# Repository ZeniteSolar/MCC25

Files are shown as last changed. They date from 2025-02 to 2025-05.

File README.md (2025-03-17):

# MCC25
MCC25  
MPPT Battery charger  

| Input Voltage | 0 ~ 21 V  |
| ---: | :--- |
| Output Voltage  | 21 ~ 40V  |
| Output Power | 200 W |
| Efficiency | > 90% |

## Modelo 3D

<p align="center">
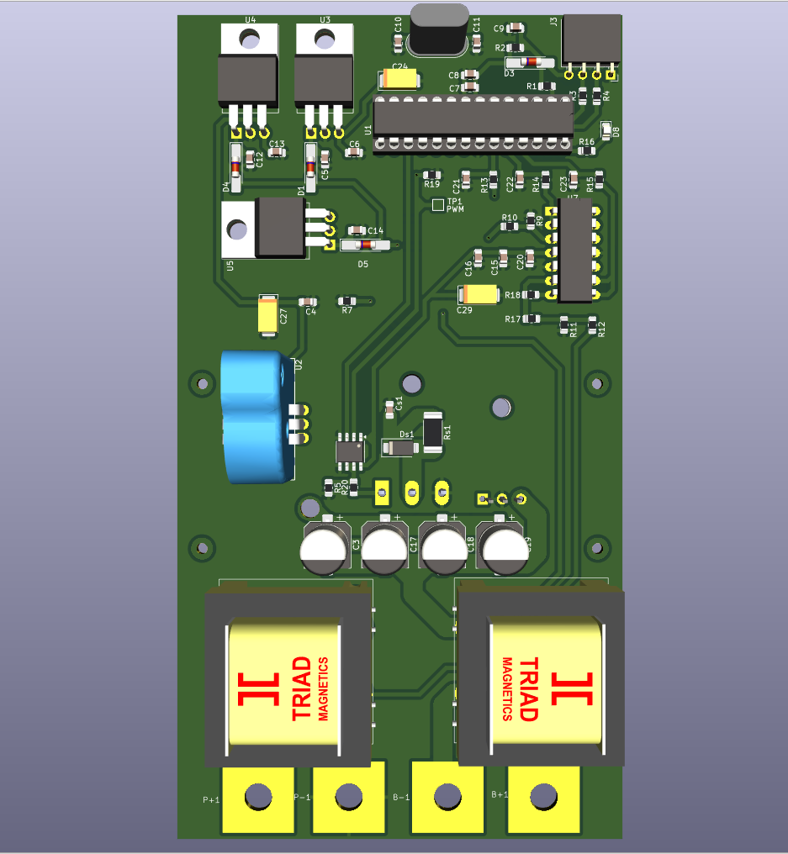
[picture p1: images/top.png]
3D Top
  
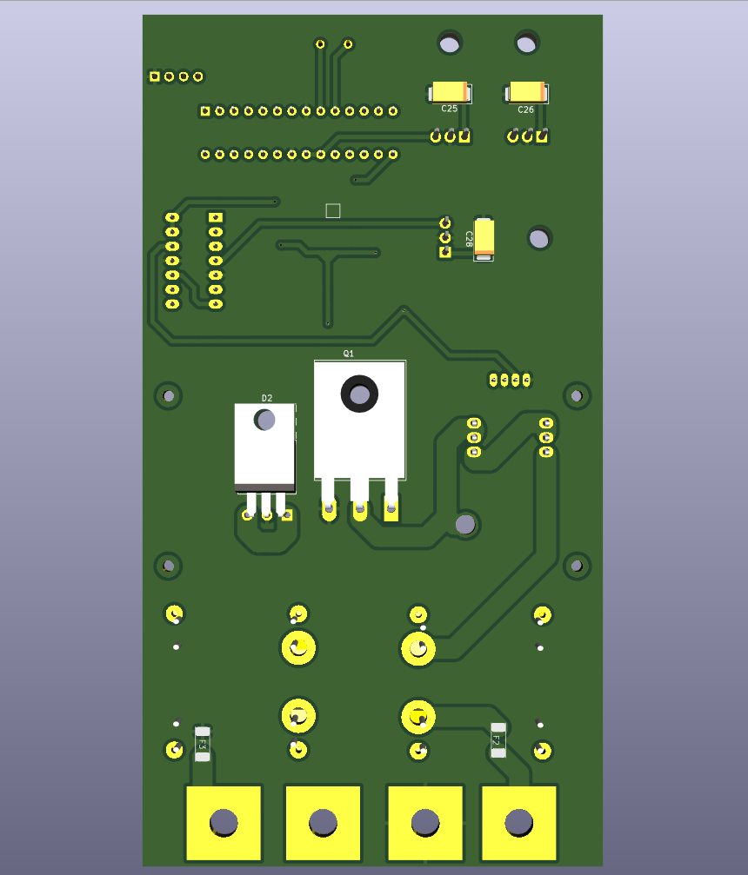
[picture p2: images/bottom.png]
3D Bottom
  
</p>

## Placa Soldada

<p align="center">
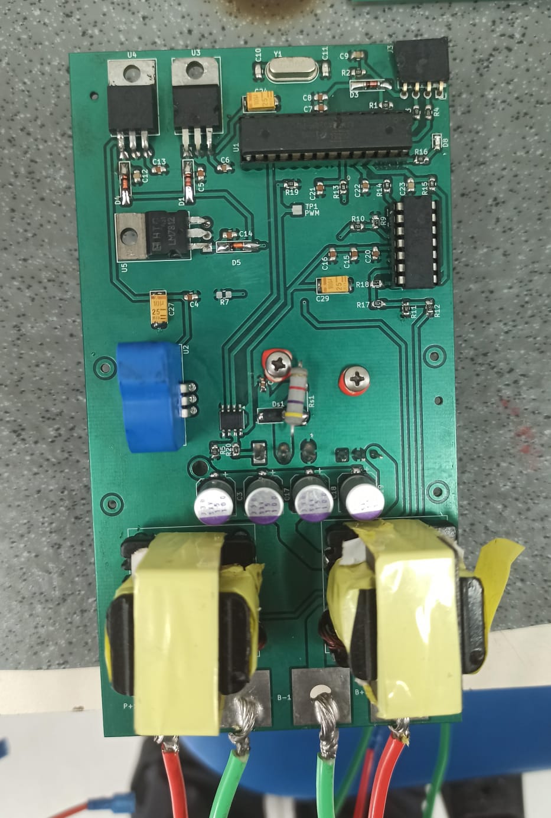
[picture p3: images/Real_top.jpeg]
Soldered Top
  
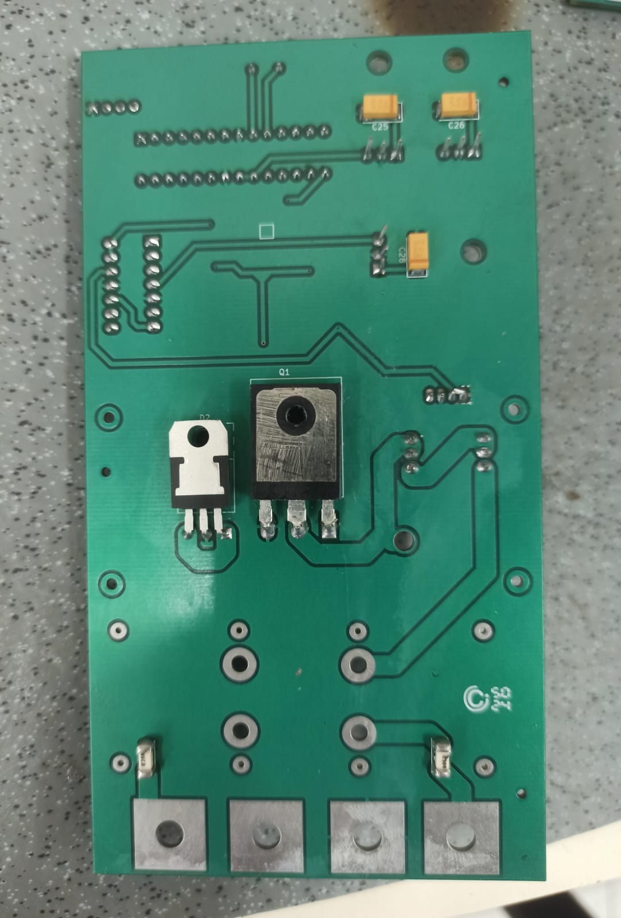
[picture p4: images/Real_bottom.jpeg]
Soldered Bottom
  
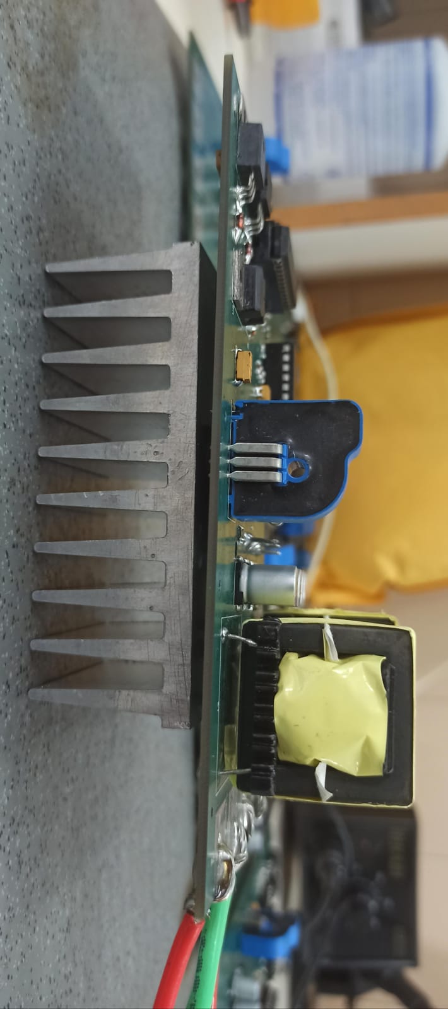
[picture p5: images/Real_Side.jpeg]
Soldered Side
  
</p>

# Guia de montagem da placa MCC25

A placa foi projetada para facilitar a montagem, mas é necessário tomar alguns cuidados devido a algumas alterações no projeto.

## Passo a Passo

| Passo | Instruções | Imagem |
|---|---|---|
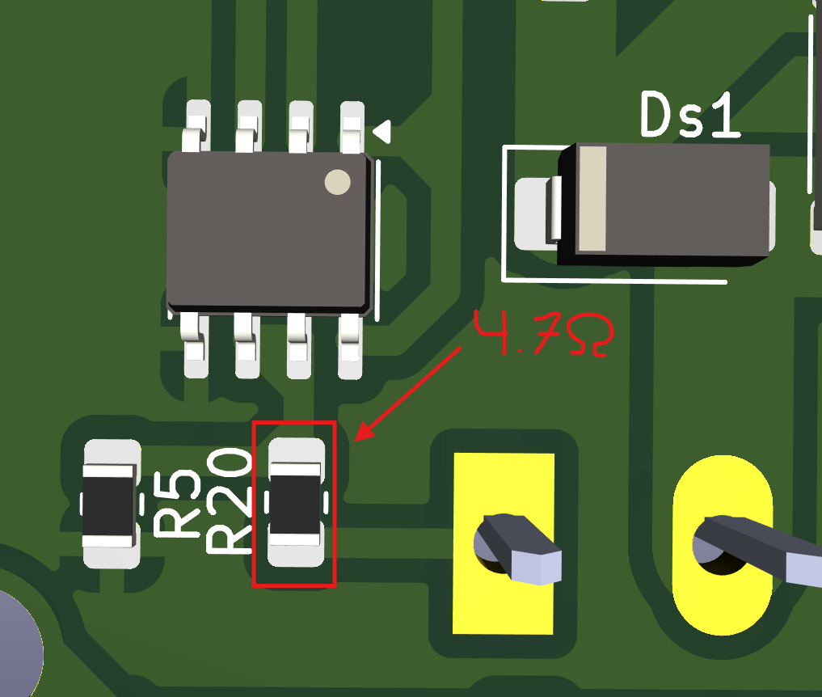
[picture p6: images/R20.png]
| **1** | Realizar a troca do resistor R20 de 15Ω para um resistor de 4.7Ω. |  |
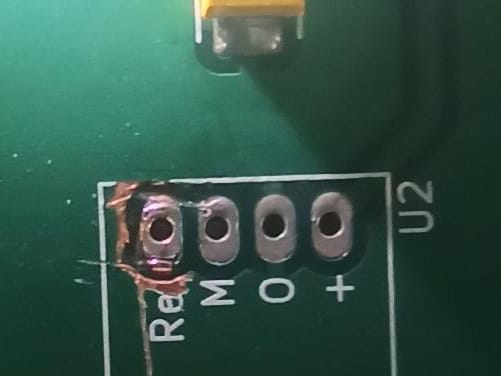
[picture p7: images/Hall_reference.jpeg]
| **2** | Isolar o pino de referência do sensor de efeito HALL "U2" raspando as trilhas conectadas ao GND, em ambos os lados da placa.( Somente raspar as trilhas relacionadas ao pino de referência, o resto manter igual ) |  |
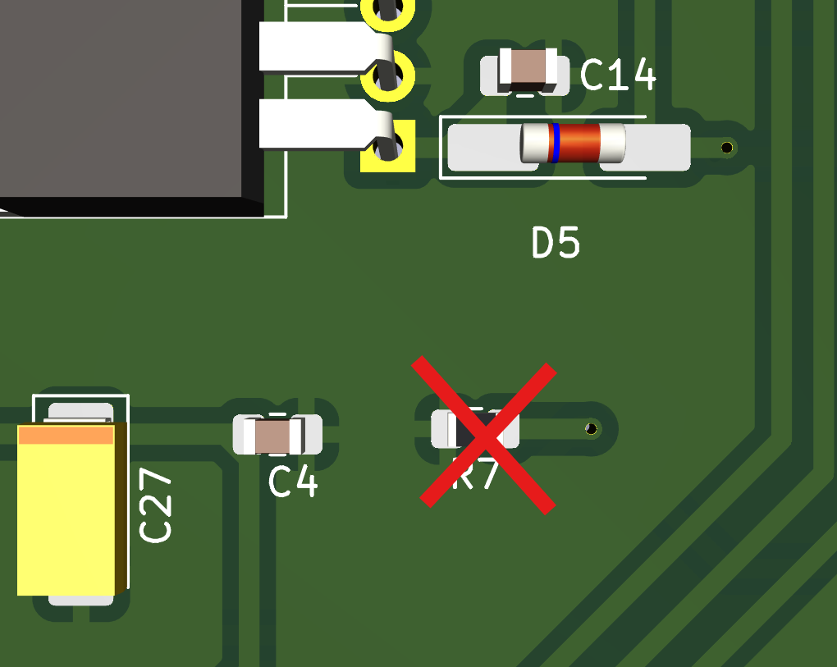
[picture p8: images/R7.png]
| **3** | Não realizar a solda do resistor R7, pois ele será soldado em outro local da placa. |  |
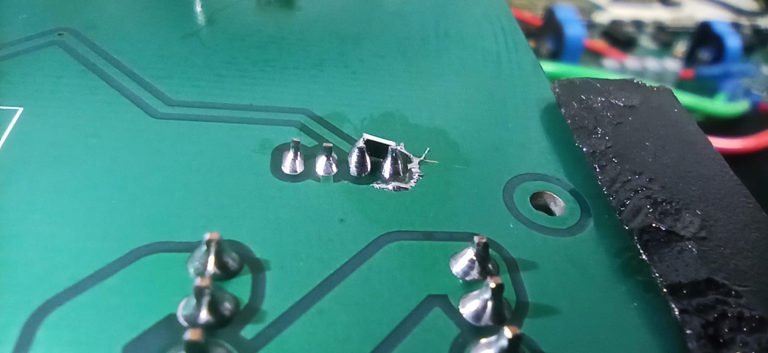
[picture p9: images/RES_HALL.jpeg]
| **4** | Após isolar o pino de referência do sensor de efeito HALL, realizar a solda dele normalmente. Em seguida, soldar um resistor de 150Ω entre o pino de referência e o output do sensor. (Certificar-se de que não há curto-circuito). |  |
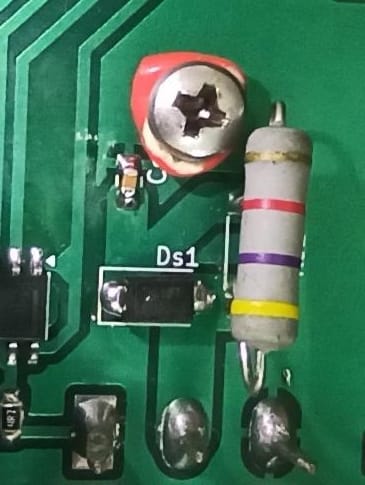
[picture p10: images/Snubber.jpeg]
| **5** | Montagem do snubber: verificar a necessidade, mas a dica de montagem é usar um diodo TVS Schottky 100V, capacitor de 4.7nF 100V e resistor 4.7KΩ 3W. |  |

## Testes

Em processo...

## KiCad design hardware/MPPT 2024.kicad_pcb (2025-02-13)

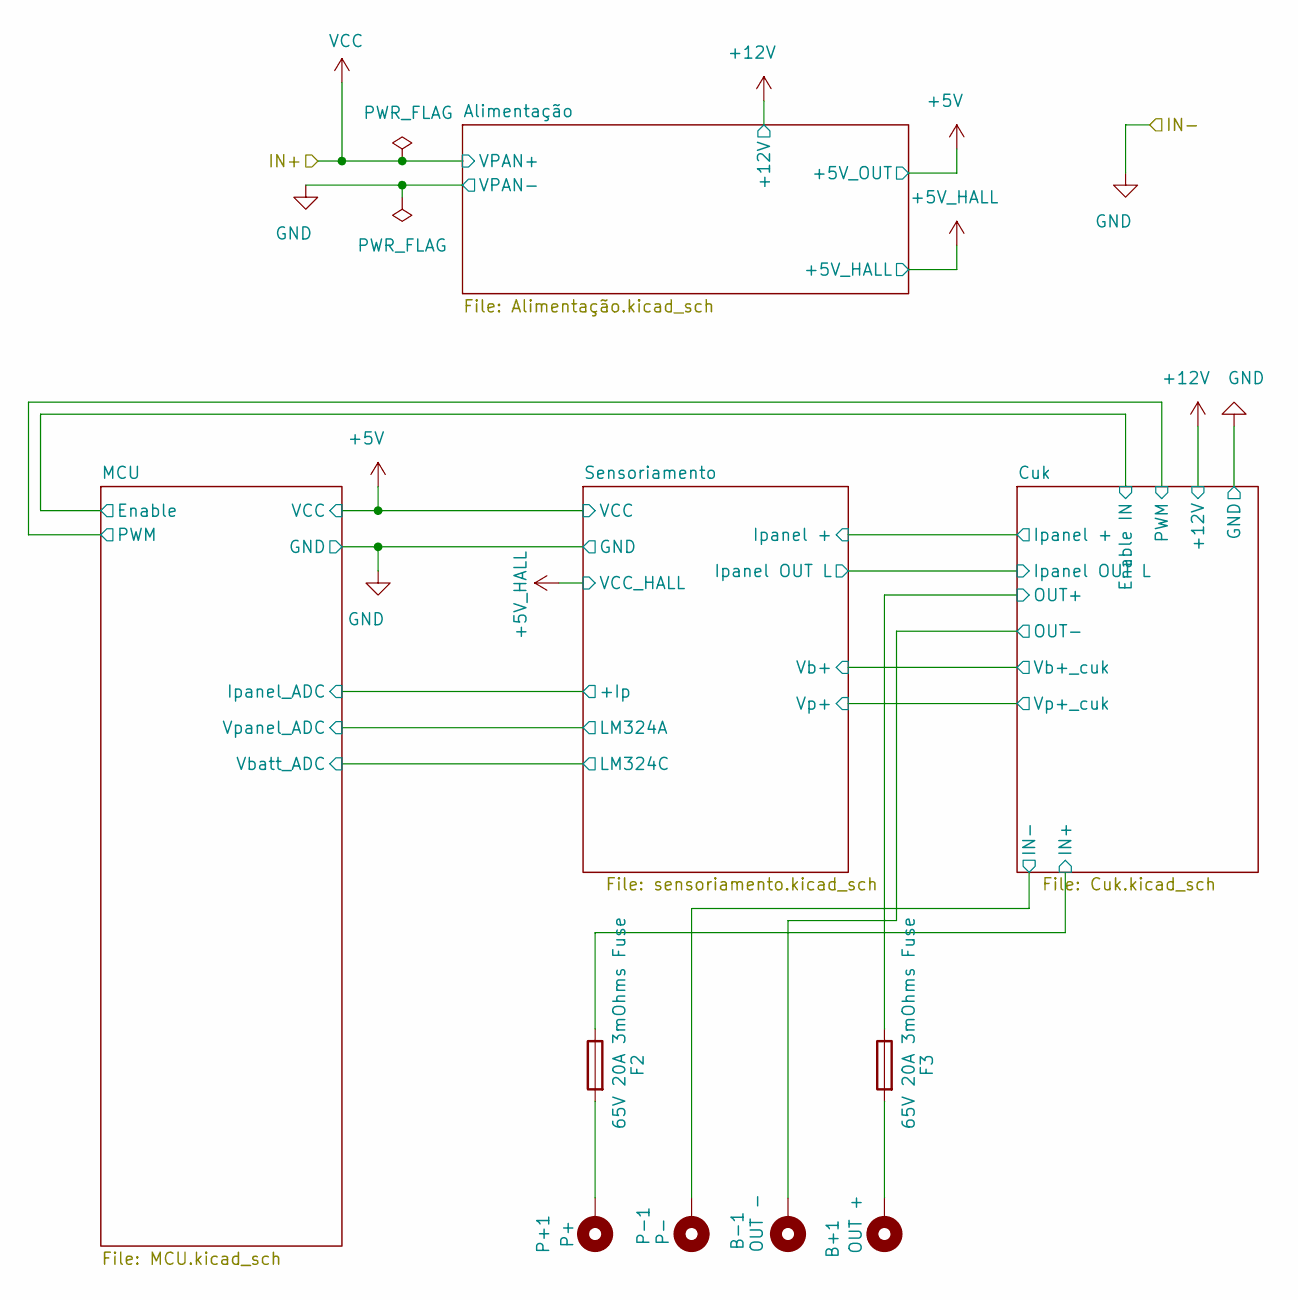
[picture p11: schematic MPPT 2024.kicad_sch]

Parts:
B+1: OUT +; FURO_PAN_BAT
B-1: OUT -; FURO_PAN_BAT
F2, F3: 65V 20A 3mOhms Fuse; FUSE_6125
P+1: P+; FURO_PAN_BAT
P-1: P-; FURO_PAN_BAT

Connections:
/Cuk/OUT-: B-1.1; also elsewhere on the board
GND: F3.1, P-1.1; also elsewhere on the board
unnamed: B+1.1, F3.2
unnamed: F2.2, P+1.1
VCC: F2.1; also elsewhere on the board

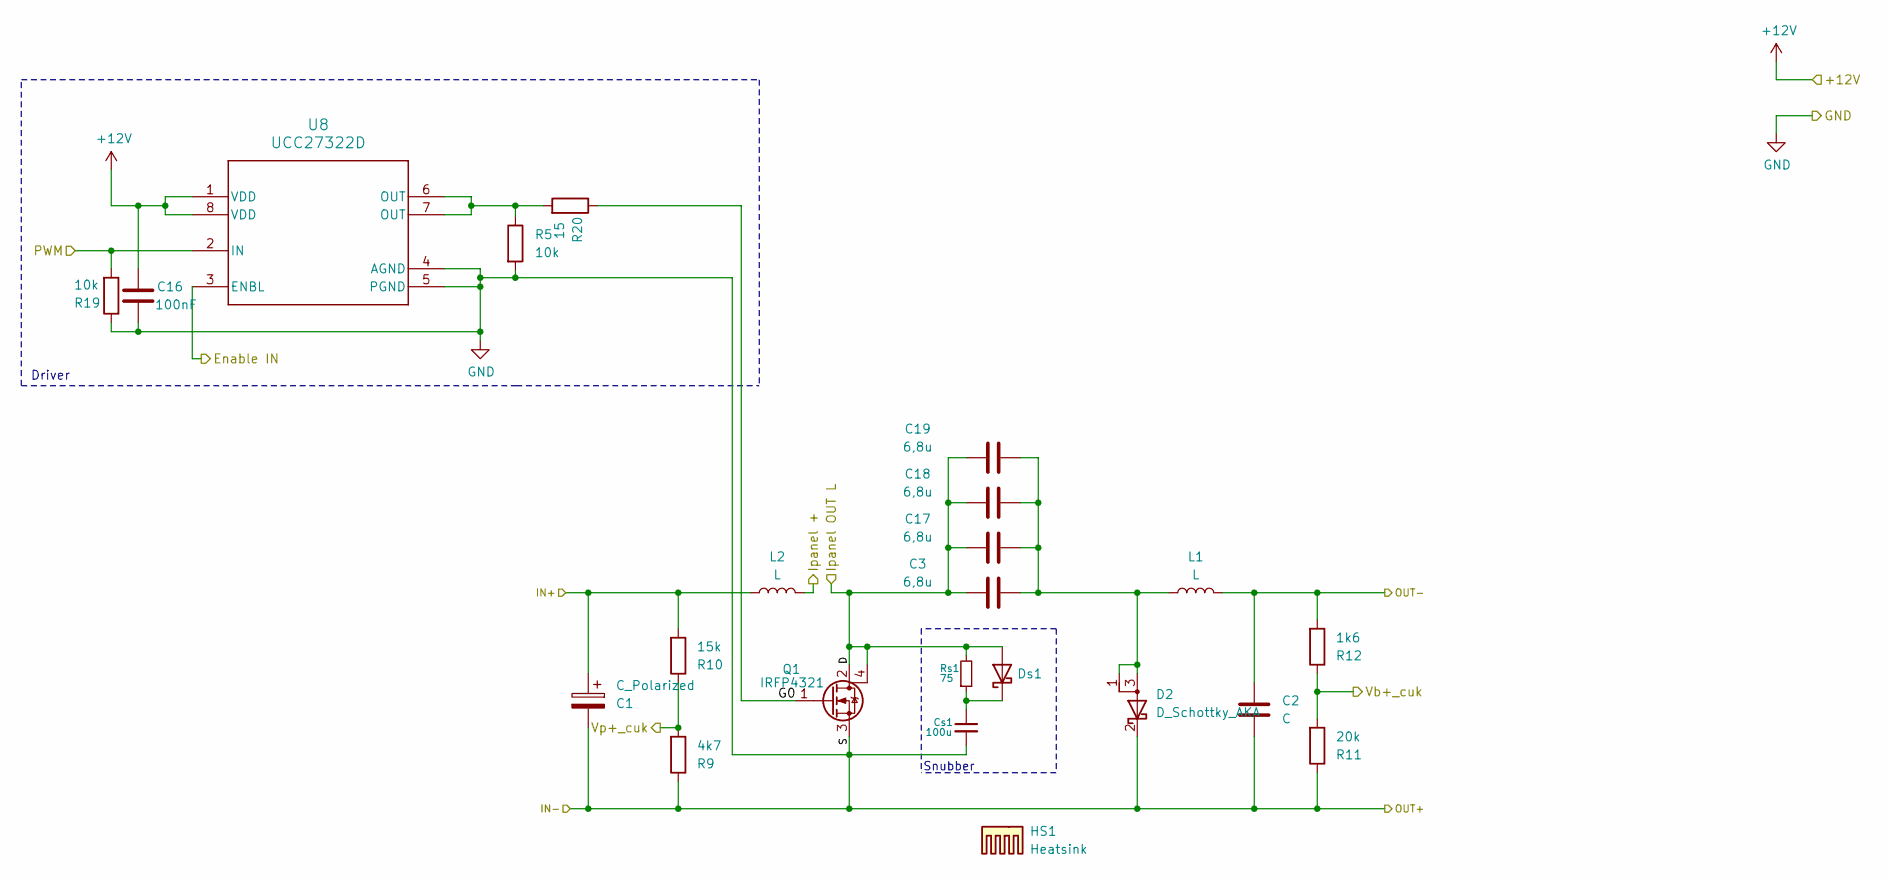
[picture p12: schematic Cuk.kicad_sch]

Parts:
C1: C_Polarized
C2: C
C3, C17, C18, C19: 6,8u; CP_Elec_8x11.9
C16: 100nF; C_0805_2012Metric_Pad1.18x1.45mm_HandSolder
Cs1: 100u; C_0805_2012Metric_Pad1.18x1.45mm_HandSolder; Voltage 200V; Tolerance 10%
D2: D_Schottky_AKA; TO-220-3_Horizontal_TabUp
Ds1: D_Schottky; D_SMA
HS1: Heatsink; DISSIPADOR
L1, L2: L; INDUTOR E30_14
Q1: IRFP4321; TO-247-3_Horizontal_TabUp
R5, R19: 10k; R_0805_2012Metric_Pad1.20x1.40mm_HandSolder
R9: 4k7; R_0805_2012Metric_Pad1.20x1.40mm_HandSolder
R10: 15k; R_0805_2012Metric_Pad1.20x1.40mm_HandSolder
R11: 20k; R_0805_2012Metric_Pad1.20x1.40mm_HandSolder
R12: 1k6; R_0805_2012Metric_Pad1.20x1.40mm_HandSolder
R20: 15; R_0805_2012Metric_Pad1.20x1.40mm_HandSolder
Rs1: 75; R_2512_6332Metric_Pad1.40x3.35mm_HandSolder; Tolerance 10%
U8: UCC27322D; SOIC-8_3.9x4.9mm_P1.27mm

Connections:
+12V: C16.2, U8.1 (VDD), U8.8 (VDD); also elsewhere on the board
/Cuk/D: C3.1, C17.1, C18.1, C19.1, Ds1.2 (A), Q1.2 (D), Q1.4 (D), Rs1.2; also elsewhere on the board
/Cuk/Enable IN: U8.3 (ENBL); also elsewhere on the board
/Cuk/G0: Q1.1 (G), R20.1
/Cuk/Ipanel +: L2.2; also elsewhere on the board
/Cuk/OUT-: C2.1, L1.2, R12.2; also elsewhere on the board
/Cuk/PWM: R19.2, U8.2 (IN); also elsewhere on the board
/Cuk/Vb+_cuk: R11.2, R12.1; also elsewhere on the board
/Cuk/Vp+_cuk: R9.2, R10.1; also elsewhere on the board
GND: C1.2, C2.2, C16.1, Cs1.2, D2.2 (K), Q1.3 (S), R5.2, R9.1, R11.1, R19.1, U8.4 (AGND), U8.5 (PGND); also elsewhere on the board
unnamed: C3.2, C17.2, C18.2, C19.2, D2.1 (A), D2.3 (A), L1.1
unnamed: Cs1.1, Ds1.1 (K), Rs1.1
unnamed: R5.1, R20.2, U8.6 (OUT), U8.7 (OUT)
VCC: C1.1, L2.1, R10.2; also elsewhere on the board

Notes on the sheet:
Snubber
Driver

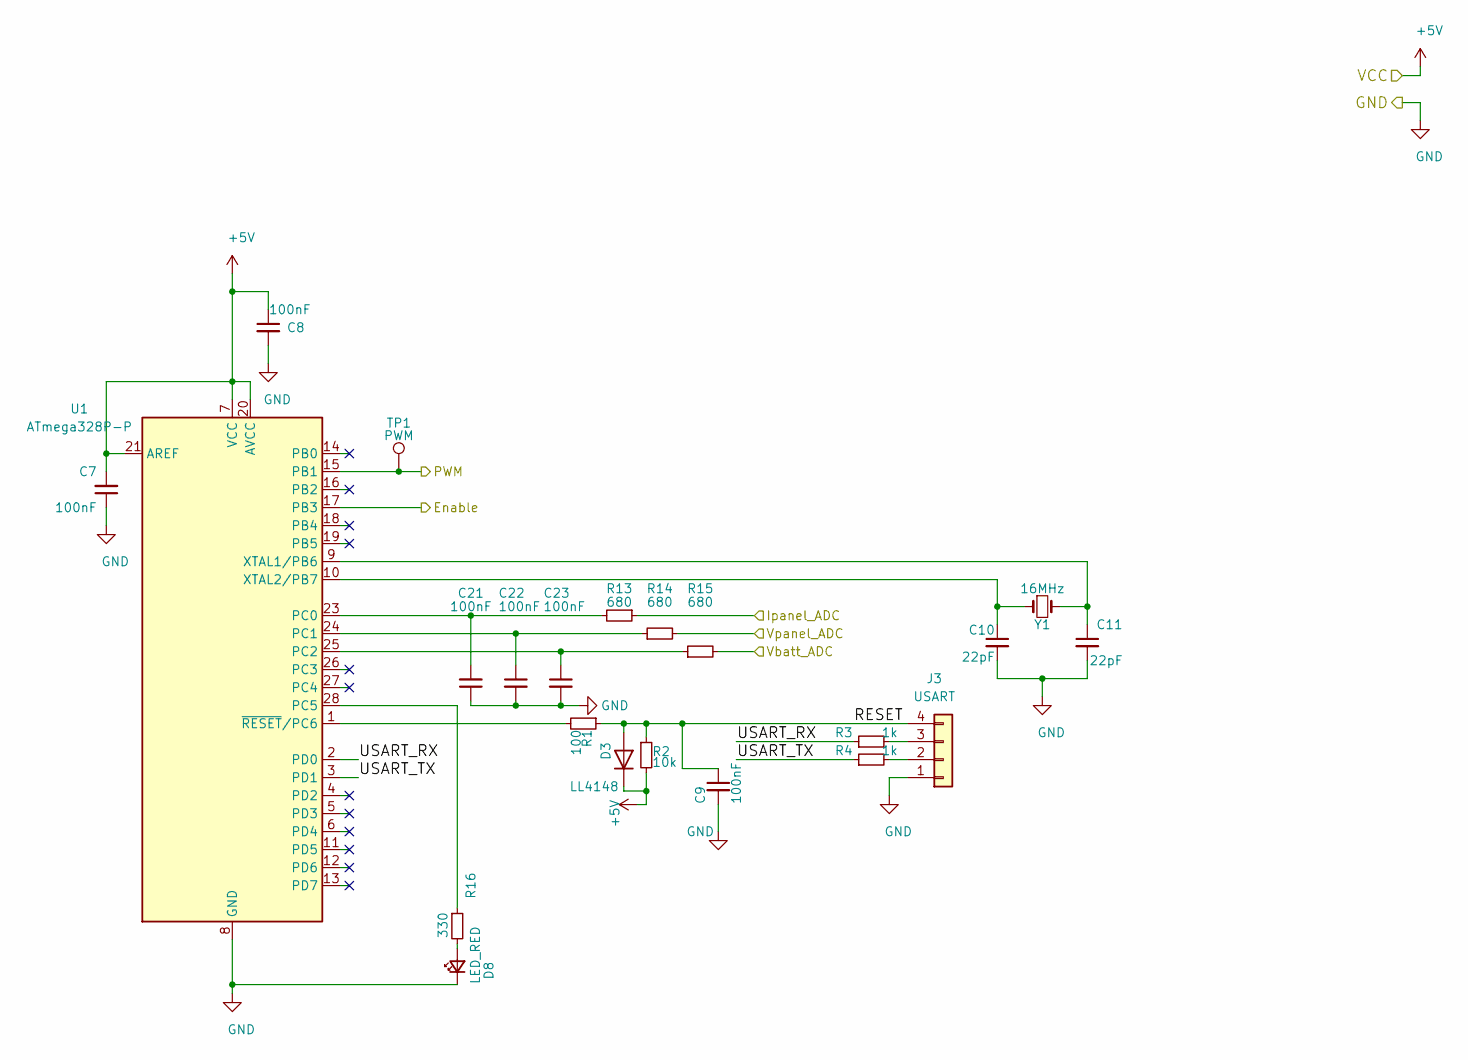
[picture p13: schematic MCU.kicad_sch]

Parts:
C7, C8, C9, C21, C22, C23: 100nF; C_0805_2012Metric_Pad1.18x1.45mm_HandSolder
C10, C11: 22pF; C_0805_2012Metric_Pad1.18x1.45mm_HandSolder
D3: LL4148; D_MiniMELF_Handsoldering
D8: LED_RED; LED_0805_2012Metric_Pad1.15x1.40mm_HandSolder
J3: USART; PinSocket_1x04_P2.54mm_Horizontal
R1: 100; R_0805_2012Metric_Pad1.20x1.40mm_HandSolder
R2: 10k; R_0805_2012Metric_Pad1.20x1.40mm_HandSolder
R3, R4: 1k; R_0805_2012Metric_Pad1.20x1.40mm_HandSolder
R13, R14, R15: 680; R_0805_2012Metric_Pad1.20x1.40mm_HandSolder
R16: 330; R_0805_2012Metric_Pad1.20x1.40mm_HandSolder
TP1: PWM; TestPoint_Pad_2.0x2.0mm
U1: ATmega328P-P; DIP-28_W7.62mm
Y1: 16MHz; Crystal_HC49-U_Vertical

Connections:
+5V: C7.2, C8.1, D3.1 (K), R2.2, U1.7 (VCC), U1.20 (AVCC), U1.21 (AREF); also elsewhere on the board
/Cuk/Enable IN: U1.17 (PB3); also elsewhere on the board
/Cuk/PWM: TP1.1, U1.15 (PB1); also elsewhere on the board
/MCU/Ipanel_ADC: R13.1; also elsewhere on the board
/MCU/RESET: C9.1, D3.2 (A), J3.4, R1.1, R2.1
/MCU/USART_RX: R3.1, U1.2 (PD0)
/MCU/USART_TX: R4.1, U1.3 (PD1)
/MCU/Vbatt_ADC: R15.2; also elsewhere on the board
/MCU/Vpanel_ADC: R14.2; also elsewhere on the board
GND: C7.1, C8.2, C9.2, C10.2, C11.2, C21.1, C22.2, C23.2, D8.1 (K), J3.1, U1.8 (GND), U1.22 (GND); also elsewhere on the board
unnamed: D8.2 (A), R16.2
unnamed: J3.2, R4.2
unnamed: J3.3, R3.2
unnamed: C21.2, R13.2, U1.23 (PC0)
unnamed: C22.1, R14.1, U1.24 (PC1)
unnamed: C23.1, R15.1, U1.25 (PC2)
unnamed: R16.1, U1.28 (PC5)
unnamed: C11.1, U1.9 (XTAL1/PB6), Y1.2
unnamed: C10.1, U1.10 (XTAL2/PB7), Y1.1
unnamed: R1.2, U1.1 (~RESET/PC6)

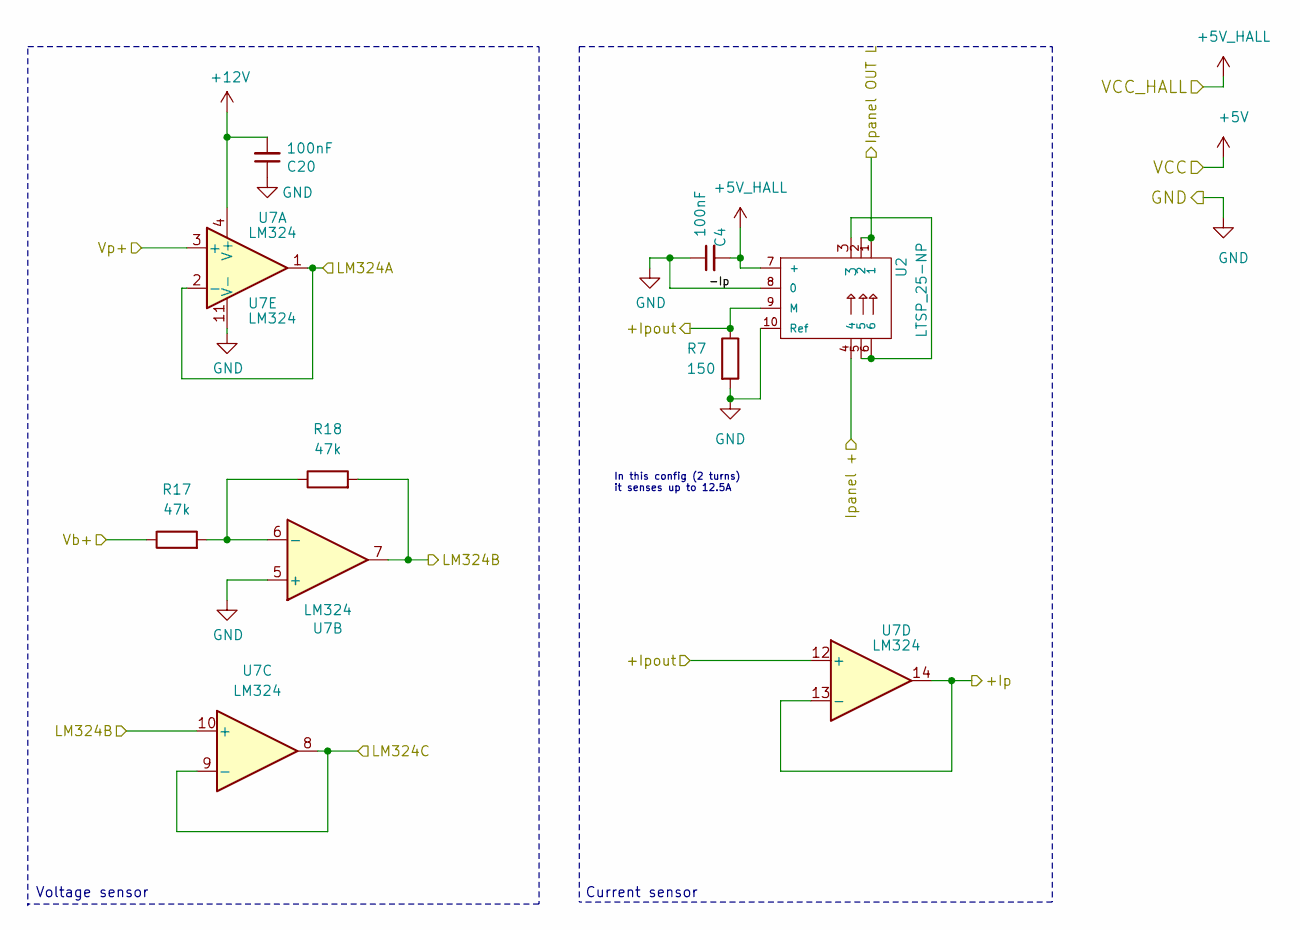
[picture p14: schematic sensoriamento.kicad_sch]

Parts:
C4, C20: 100nF; C_0805_2012Metric_Pad1.18x1.45mm_HandSolder
R7: 150; R_0805_2012Metric_Pad1.20x1.40mm_HandSolder
R17, R18: 47k; R_0805_2012Metric_Pad1.20x1.40mm_HandSolder
U2: LTSP_25-NP
U7: LM324; DIP-14_W7.62mm_LongPads

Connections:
+5V_HALL: C4.2, U2.7 (+); also elsewhere on the board
+12V: C20.2, U7.4 (V+); also elsewhere on the board
/Cuk/D: U2.1, U2.2; also elsewhere on the board
/Cuk/Ipanel +: U2.4; also elsewhere on the board
/Cuk/Vb+_cuk: R17.1; also elsewhere on the board
/Cuk/Vp+_cuk: U7.3 (+); also elsewhere on the board
/MCU/Ipanel_ADC: U7.13 (-), U7.14; also elsewhere on the board
/MCU/Vbatt_ADC: U7.8, U7.9 (-); also elsewhere on the board
/MCU/Vpanel_ADC: U7.1, U7.2 (-); also elsewhere on the board
/Sensoriamento/+Ipout: R7.1, U2.9 (M), U7.12 (+)
/Sensoriamento/LM324B: R18.2, U7.7, U7.10 (+)
GND: C4.1, C20.1, R7.2, U2.8 (0), U2.10 (Ref), U7.5 (+), U7.11 (V-); also elsewhere on the board
unnamed: U2.3, U2.5, U2.6
unnamed: R17.2, R18.1, U7.6 (-)

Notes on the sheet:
In this config (2 turns) it senses up to 12.5A
Voltage sensor
Current sensor

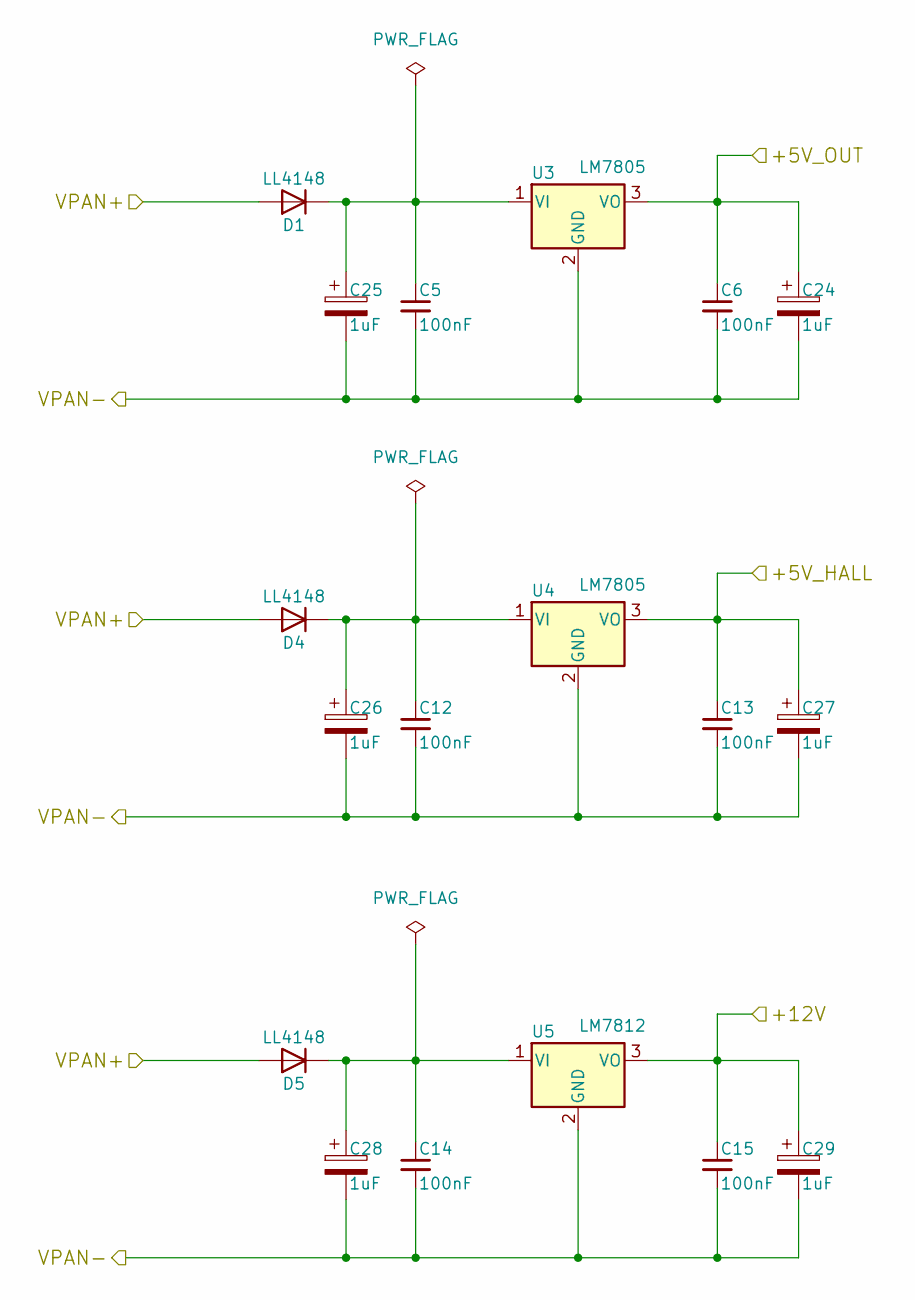
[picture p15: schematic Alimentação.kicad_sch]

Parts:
C5, C6, C12, C13, C14, C15: 100nF; C_0805_2012Metric_Pad1.18x1.45mm_HandSolder
C24, C25, C26, C27, C28, C29: 1uF; CP_EIA-6032-15_Kemet-U_Pad2.25x2.35mm_HandSolder
D1, D4, D5: LL4148; D_MiniMELF_Handsoldering
U3, U4: LM7805; TO-220-3_Horizontal_TabDown
U5: LM7812; TO-220-3_Horizontal_TabDown

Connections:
+5V: C6.1, C24.1, U3.3 (VO); also elsewhere on the board
+5V_HALL: C13.1, C27.1, U4.3 (VO); also elsewhere on the board
+12V: C15.1, C29.1, U5.3 (VO); also elsewhere on the board
GND: C5.2, C6.2, C12.2, C13.2, C14.2, C15.2, C24.2, C25.2, C26.2, C27.2, C28.2, C29.2, U3.2 (GND), U4.2 (GND), U5.2 (GND); also elsewhere on the board
unnamed: C5.1, C25.1, D1.1 (K), U3.1 (VI)
unnamed: C12.1, C26.1, D4.1 (K), U4.1 (VI)
unnamed: C14.1, C28.1, D5.1 (K), U5.1 (VI)
VCC: D1.2 (A), D4.2 (A), D5.2 (A); also elsewhere on the board

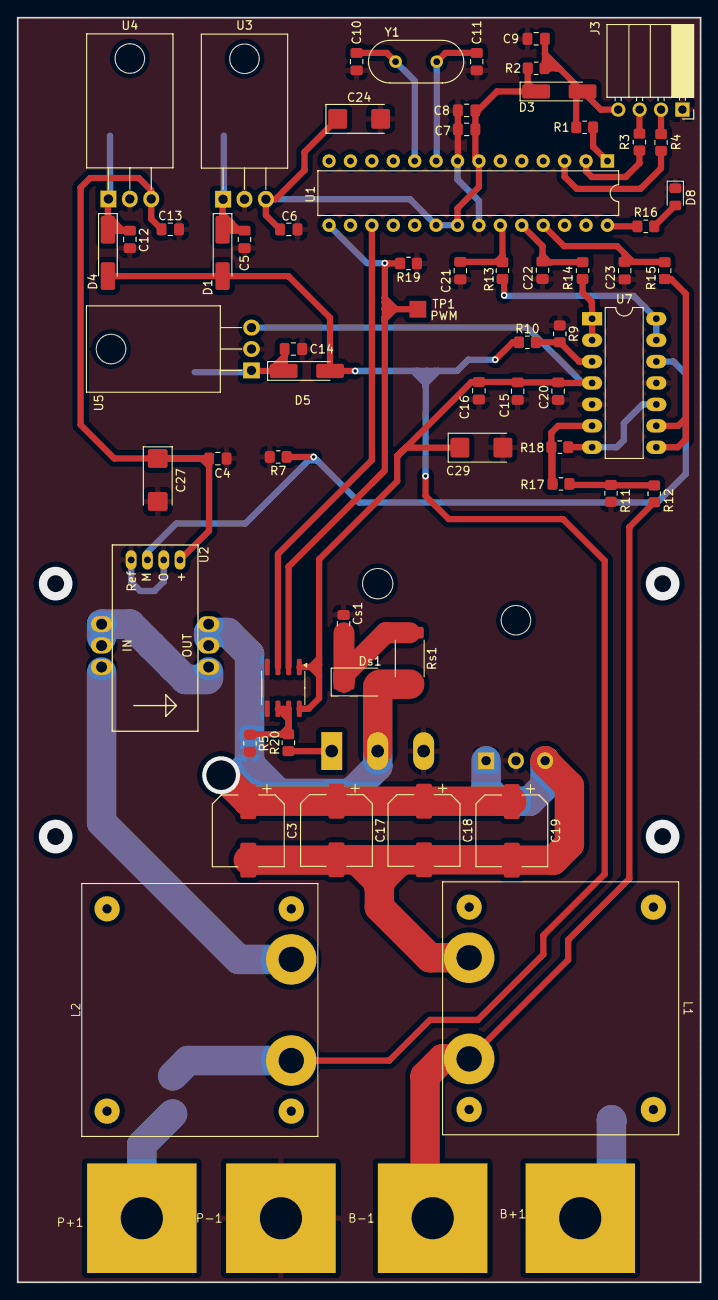
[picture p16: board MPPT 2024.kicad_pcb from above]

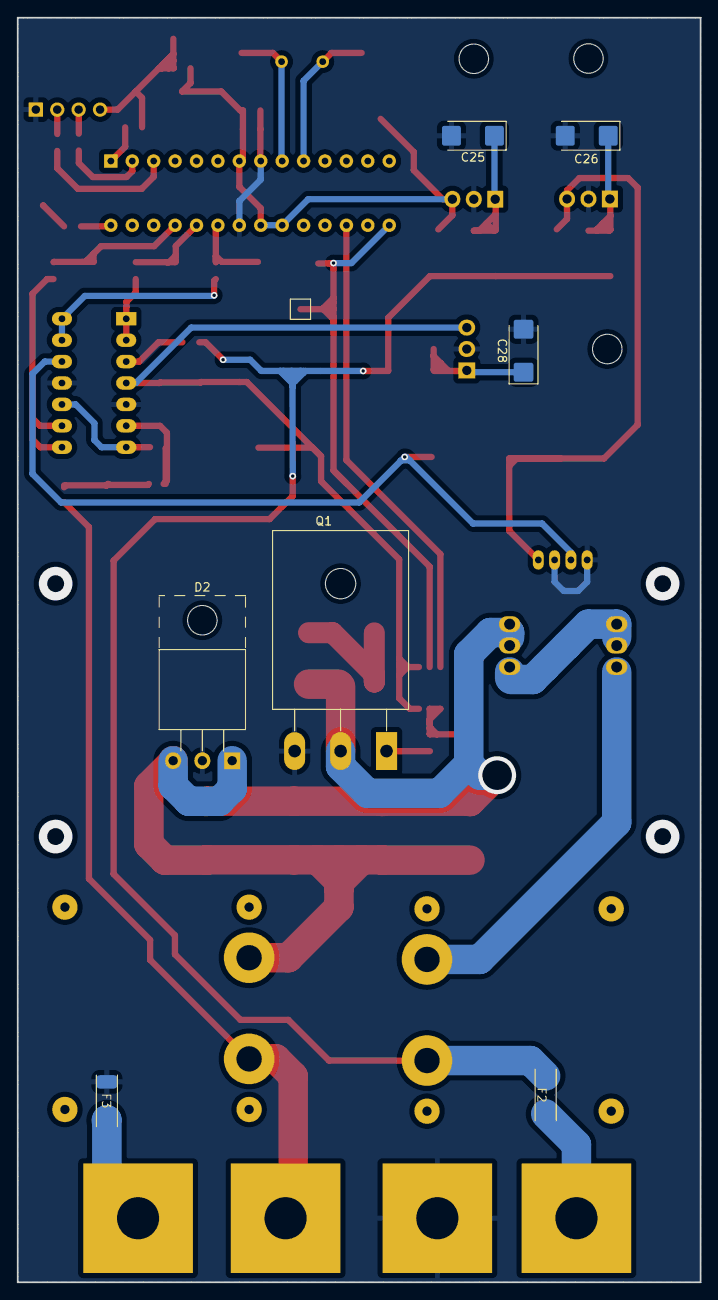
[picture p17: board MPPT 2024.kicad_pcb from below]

Board: 2 copper layers, 81.0 x 150.0 mm, 73 parts (8 on the bottom side), 41 nets.

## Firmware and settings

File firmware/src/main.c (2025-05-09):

#ifndef __AVR_ATmega328P__
    #define __AVR_ATmega328P__
#endif

#ifndef F_CPU
#define F_CPU 16000000UL
#endif

#include "main.h"

int main(void)
{
    #ifdef USART_ON
    usart_init(UBRR_VALUE,1,1);                         // inicializa a usart
    usart_send_string("\n\n\nUSART... OK!\n");
    #endif

    _delay_ms(1000);

    #ifdef PWM_ON
    usart_send_string("PWM...");
    pwm_init();
    set_EN_driver();
    usart_send_string(" OK!\n");
    #endif

    #ifdef ADC_ON
    usart_send_string("ADC...");
    adc_init();
    usart_send_string(" OK!\n");
    #else
    usart_send_string("ADC... OFF!\n");
    #endif

    #ifdef WATCHDOG_ON
    usart_send_string("WATCHDOG...");
    wdt_init();
    usart_send_string(" OK!\n");
    #else
    usart_send_string("WATCHDOG... OFF!\n");
    #endif

    #ifdef MACHINE_ON
    usart_send_string("MACHINE...");
    machine_init();
    state_machine = STATE_INITIALIZING;
    usart_send_string(" OK!\n");
    #else
    usart_send_string("MACHINE... OFF!\n");
    #endif

    sei();
    while(1){
       // #ifdef WATCHDOG_ON
          //  wdt_reset();
		//#endif

        #ifdef MACHINE_ON
            machine_run();
        #endif

    }
    return 0;
}

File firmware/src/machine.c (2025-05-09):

#include "machine.h"
#include "usart.h"
#include "pwm.h"


volatile control_t control;
volatile error_flags_t error_flags;
volatile state_machine_t state_machine;
void machine_init(void)
{
    TCCR2A  =   (1 << WGM21) | (0 << WGM20)         // Timer 2 in Mode 2 = CTC (clear on compar  e)
            | (0 << COM2A1) | (0 << COM2A0)         // do nothing with OC2A
            | (0 << COM2B1) | (0 << COM2B0);        // do nothing with OC2B
    TCCR2B  =   (0 << WGM22)                        // Timer 0 in Mode 2 = CTC (clear on compar  e)
            | (0 << FOC0A) | (0 << FOC0B)           // dont force outputs
            | (1 << CS22)                           // clock enabled, prescaller = 1024
            | (1 << CS21)
            | (1 << CS20);
    OCR2A   =   66;                              // Valor para igualdade de comparacao A par  a frequencia de 150 Hz
    TIMSK2 |=   (1 << OCIE2A);                      // Ativa a interrupcao na igualdade de comp  aração do TC2 com OCR2A
	//TODO revisar isso
} 

void check_buffers(void)
{
    //VERBOSE_MSG_MACHINE(usart_send_string("Checking buffers..."));
    while(!CBUF_IsFull(cbuf_adc0));
    while(!CBUF_IsFull(cbuf_adc1));
    while(!CBUF_IsFull(cbuf_adc2));
    //VERBOSE_MSG_ERROR(usart_send_string("<No buffers to check>"));
    //VERBOSE_MSG_MACHINE(usart_send_string(" \t\tdone.\n")); 
}

void check_panel_voltage(void)
{
    if(control.v_panel[0] >= MAXIMUM_PANEL_VOLTAGE){
        error_flags.overvolt_panel = 1;
    }
    else if(control.v_panel[0] <= MINIMUM_PANEL_VOLTAGE){
        error_flags.undervolt_panel = 1;
    }
    else{
        error_flags.overvolt_panel = 0;
        error_flags.undervolt_panel = 0;
        error_flags.overvoltage = 0;
        error_flags.undervoltage = 0;
    }
}

void check_panel_current(void)
{
    if(control.i_panel[0] >= MAXIMUM_PANEL_CURRENT)
    {
        error_flags.overcurrent = 1;
    }
    else{
        error_flags.overcurrent = 0;
    }
}
void check_batt_voltage(void){
    if(control.v_batt[0] >= MAXIMUM_BATT_VOLTAGE){
        error_flags.overvoltage = 1;
    } else if(control.v_batt[0] <= MINIMUM_BATT_VOLTAGE){
        error_flags.undervoltage = 1;
    } else{
        error_flags.overvoltage = 0;
        error_flags.undervoltage = 0;
    }
}
void read_and_check_adcs(void){
#ifdef ADC_ON
    control.i_panel[0] = ipanel_to_float(ma_adc0());
    control.v_panel[0] = vpanel_to_float(ma_adc1());

    //control.vbatt = vbaterry_to_float(ma_adc2); //TODO terminar
    switch(state_machine){
        case STATE_INITIALIZING:
            check_panel_voltage();
            check_panel_current();
            //check_batt_voltage();

            break;
        case STATE_RUNNING:
            check_panel_voltage();
            check_panel_current();
            //check_batt_voltage();

            break;      
        default:
            break;
    }
#endif
}

void set_LED(void){
    set_bit(LED_DDR, LED);
    set_bit(LED_PORT, LED);
}

void set_EN_driver(void){
    set_bit(ENABLE_DRIVER_DDR, ENABLE_DRIVER);
    set_bit(ENABLE_DRIVER_PORT, ENABLE_DRIVER);
}

void clr_EN_driver(void){
    clr_bit(ENABLE_DRIVER_PORT, ENABLE_DRIVER);
}

void task_initializing(void){
    //control.i_panel[0] = ipanel_to_float(ma_adc0());
    //control.v_panel[0] = vpanel_to_float(ma_adc1());
    set_LED();
    control.sweep_done = 0;
    //sweep(); --> Fazer uma varredura para encontrar a melhor faixa de operação

    //Verificando os limites elétricos
    //check_buffers();
    check_panel_voltage(); 
    check_panel_current();
    //check_batt_voltage();
    //set_EN_driver();

    if(!error_flags.all){
        usart_send_string("Inicializando o sistema!\n");
        state_machine = STATE_RUNNING;
    }else{
        usart_send_string("Não foi possível inicializar!\n");
        state_machine = STATE_ERROR;
    }
}
void task_running(void){
    check_panel_voltage(); 
    check_panel_current();
    //check_batt_voltage();
    
    #ifdef PWM_ON
        pwm_compute();
    #endif


    // TODO add usart msgs

    //chamar o check limites eletricos 
    //TODO logica de primeira corrida
        //sweep duty inicial 
    //P&O
    //COnsider duty limit
        // set duty  
    

}
void task_error(void){
    #ifdef PWM_ON
        pwm_reset();
        clr_bit(LED_PORT,LED);
    #endif

    total_errors++;         // incrementa a contagem de erros
    usart_send_string("The error code is: ");
    usart_send_uint16(error_flags.all);
    usart_send_char('\n');

    if(error_flags.overcurrent)
        usart_send_string("\t - Panel over-current!\n");
    if(error_flags.overvoltage)
        usart_send_string("\t - Battery over-voltage!\n");
    if(error_flags.undervolt_panel)
        usart_send_string("\t - Panel under-voltage!\n");
    if(error_flags.undervoltage)
        usart_send_string("\t - Baterry under-voltage!\n");
    if(!error_flags.all)
        usart_send_string("\t - Oh no, it was some unknown error.\n");

    usart_send_string("The error level is: ");
    usart_send_uint16(total_errors);
    usart_send_char('\n');

    if(total_errors < 2){
        usart_send_string("I will reset the machine state.\n");
    }
    if(total_errors >= 20){
        usart_send_string("The watchdog will reset the whole system.\n");
        for(;;);    // waits the watchdog to reset.
    }
 
    state_machine = STATE_INITIALIZING;

}

void machine_run(void){
    //#define MACHINE_CLK_DIVIDER_VALUE           10
    //static uint8_t machine_clk_divider = 0;
    if(machine_clk){
        machine_clk = 0;
        //if(machine_clk_divider++ == MACHINE_CLK_DIVIDER_VALUE){
           // machine_clk_divider = 0;
            if(adc_data_ready){
                adc_data_ready = 0;
                read_and_check_adcs();

                usart_send_string(" Vpanel Buffer: ");
                usart_send_float(control.v_panel[0], 4);
                usart_send_string(" Ipanel Buffer: ");
                usart_send_float(control.i_panel[0], 4);
                usart_send_string(" D buffer: ");
                usart_send_uint16(control.D);
                usart_send_char('\n');
            } 

            switch(state_machine){
                case STATE_INITIALIZING:
                    task_initializing();

                    break;
                case STATE_RUNNING:
                    task_running();

                    break;
                case STATE_ERROR:
                    task_error();

                default:
                    break;
            }
        //}
    }
/*     usart_send_string("Ipanel: ");
    usart_send_float(control.i_panel[0], 4);
    usart_send_string("Vpanel: ");
    usart_send_float(control.v_panel[0],4);
    usart_send_string("Vbatt: ");
    usart_send_uint16(ma_adc2());
    usart_send_char('\n');*/

}
ISR(TIMER2_COMPA_vect)
{
    //if(machine_clk) usart_send_string("\nERROR: CLOCK CONFLICT!!!\n");
	machine_clk = 1;
}

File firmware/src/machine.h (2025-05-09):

#ifndef __AVR_ATmega328P__
    #define __AVR_ATmega328P__
#endif

#ifndef MACHINE_H
#define MACHINE_H 

#include <avr/io.h>
#include <avr/wdt.h>
#include"conf.h"

// #ifdef USART_ON
// #include "usart.h"
// #endif
#ifdef ADC_ON
#include "adc.h"
#endif

//DEFINIÇÕES DE MEDIDAS
#define MAXIMUM_PANEL_CURRENT 11.0f //11A
#define MAXIMUM_PANEL_VOLTAGE 24.0f // 21V
#define MAXIMUM_BATT_VOLTAGE 60.0f // 60V
#define MINIMUM_BATT_VOLTAGE 33.0f //33V
#define MINIMUM_PANEL_VOLTAGE 9.0f //9V

//DEFINIÇÕES GERAIS
#define LED PC5
#define LED_DDR DDRC
#define LED_PORT PORTC
#define ENABLE_DRIVER PB3
#define ENABLE_DRIVER_DDR DDRB
#define ENABLE_DRIVER_PORT PORTB

volatile uint8_t machine_clk;
uint8_t total_errors;   // Contagem de ERROS

typedef enum state_machine{
    STATE_INITIALIZING,
    STATE_RUNNING,
    STATE_ERROR,
} state_machine_t;

extern volatile state_machine_t state_machine;

typedef struct control{
    uint8_t    D;              // value converted from 0 to TOP
    uint8_t  sweep_done;
    float    i_panel[2];              // value of panel current in AMPS
    float    v_panel[2];              // value of panel voltage in VOLTS
	float	v_batt[2];			// value of battery voltage in VOLTS
	float	pi[2];			// value of power in WATTS

}control_t;

extern volatile control_t control;

typedef union error_flags{
    struct{
        uint8_t     overcurrent :1;
        uint8_t     overvoltage :1;
		uint8_t		undervoltage:1;
		uint8_t		overvolt_panel:1;
		uint8_t		undervolt_panel:1;
    };
    uint8_t   all;
}error_flags_t;
extern volatile error_flags_t error_flags;

void machine_init(void);
void check_buffers(void);
void check_panel_voltage(void);
void check_panel_current(void);
void check_batt_voltage(void);
void read_and_check_adcs(void);
void clr_EN_driver(void);
void set_EN_driver(void);
void set_LED(void);
void task_initializing(void);
void task_running(void);
void task_error(void);
void machine_run(void);

//control.i_panel = ma_adc0(void);
//control.v_panel = ma_adc1(void);
//control.v_batt = ma_adc2(void);

#endif /* ifndef MACHINE_H */
